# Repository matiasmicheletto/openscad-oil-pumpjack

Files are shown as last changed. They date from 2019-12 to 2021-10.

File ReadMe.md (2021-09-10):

# Parametric 3D model of an oil pumpjack

This is a Code-CAD based project that consists on the parametric modeling of all the parts of a scale oil pumpjack to be 3D-printed and driven by a 5V stepper motor. 

<p align="center">
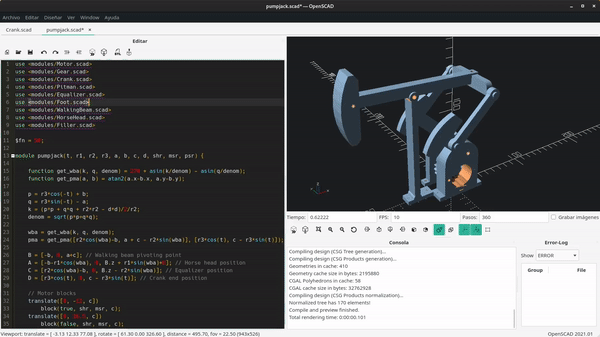
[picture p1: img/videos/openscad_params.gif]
Model
  
</p>

## Parameters of the model

This design is not based on any real model. Some basic parameters were selected to define the mechanical system dimensions.

<p align="center">
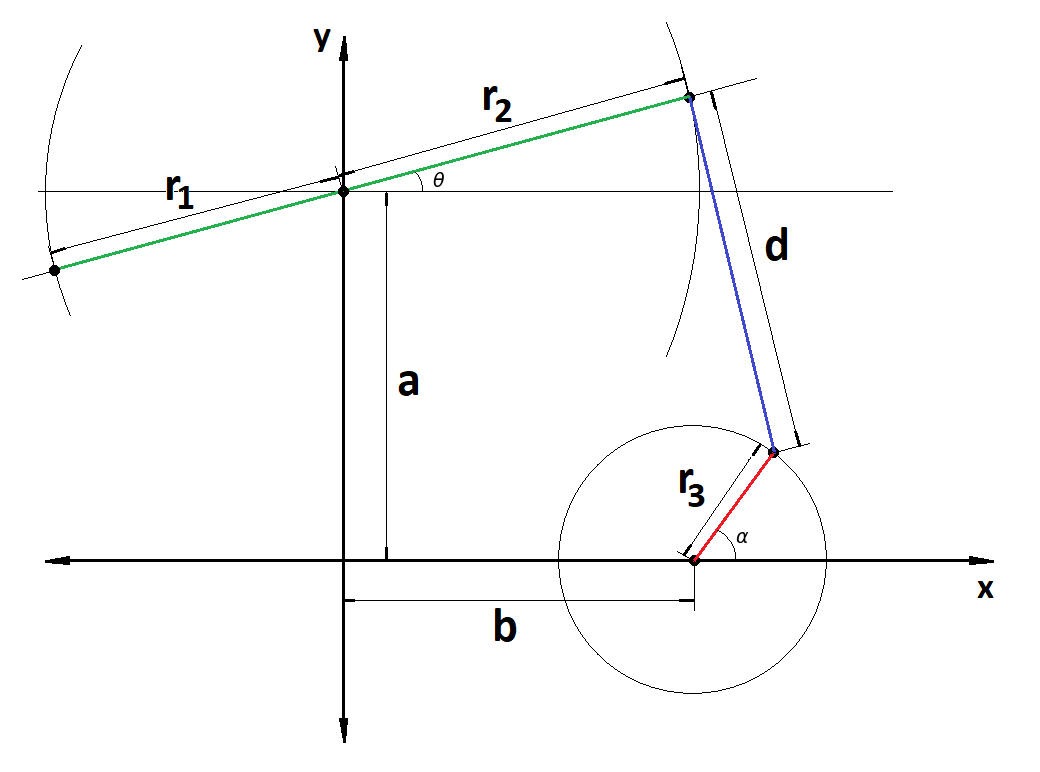
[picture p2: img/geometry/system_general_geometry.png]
Dimensions
  
</p>

An Octave simulation was used to test the resulting behavior of the machine depending on the selected parameters. The script was intended to optimize the design in some way and can be extended to perform a structural or a performance analysis.  

<p align="center">
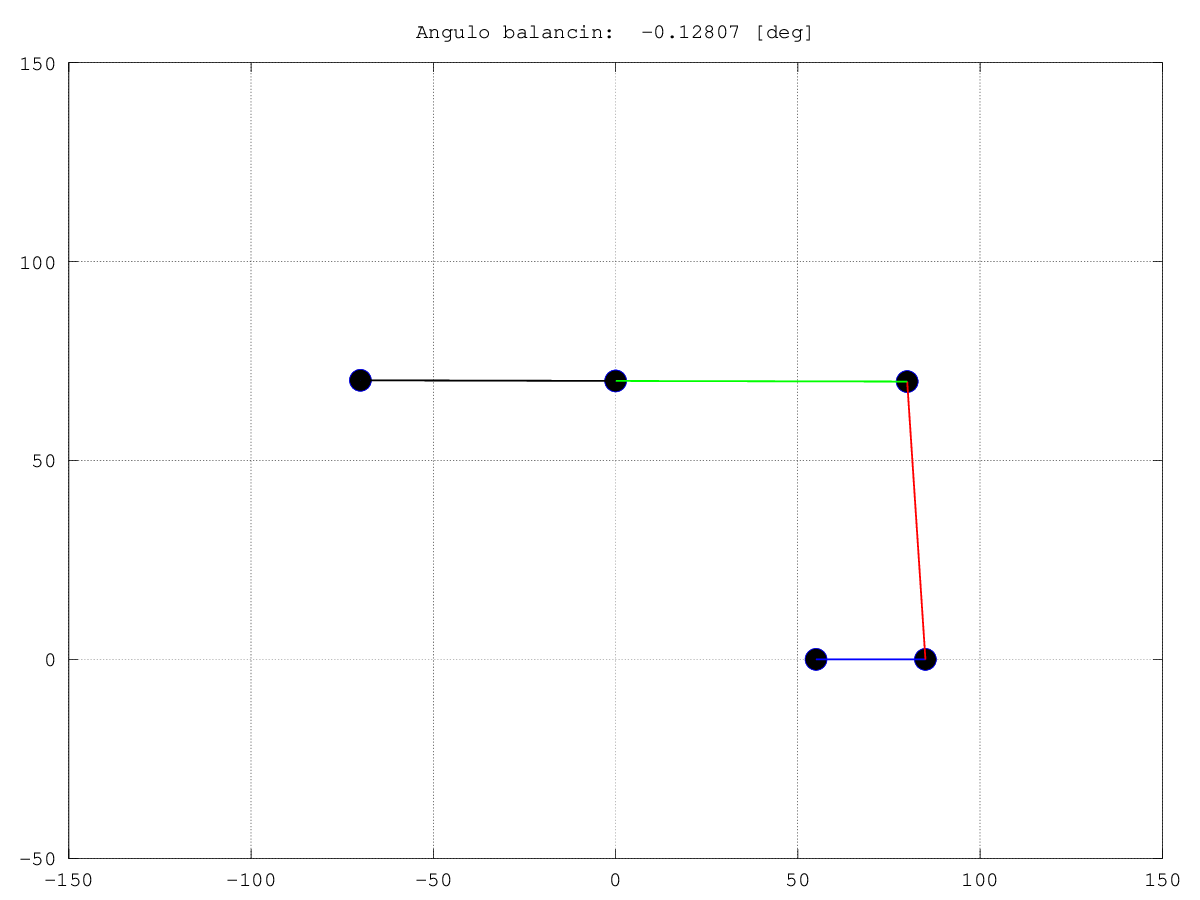
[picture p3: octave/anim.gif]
Simulation
  
</p>

## Electronics 

To control the stepper motor position and speed, it is provided the design of a four-step sequencer that uses a two-bit counter based on JK master-slave flip-flops (74HC109) and an AND-gate based decoder (74HC08). A ULN2003 based driver (not displayed in the schematics) was used to amplify the output current of the sequencer.  

<p align="center">
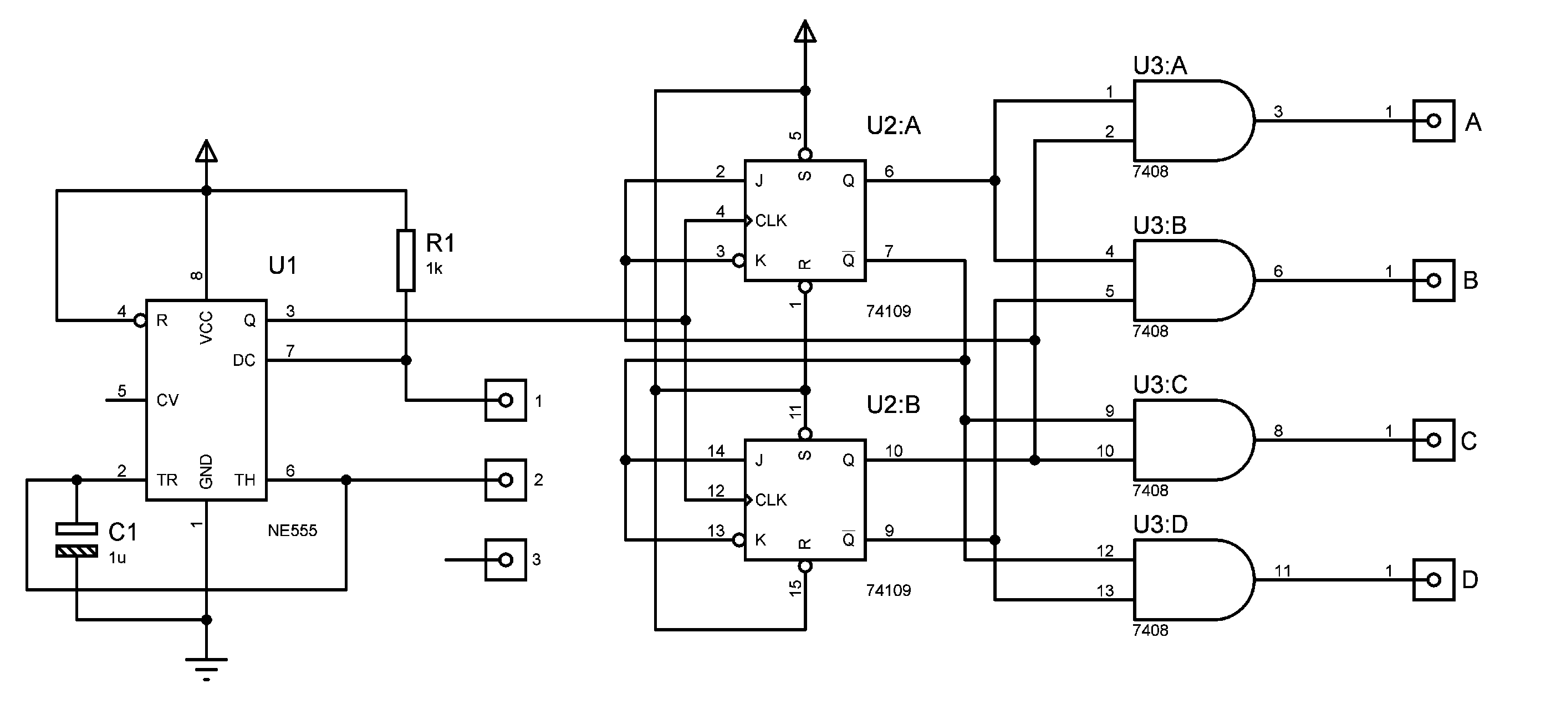
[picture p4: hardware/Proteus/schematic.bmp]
Schematics
  
</p>

This circuit was implemented on a perfboard. A CAD PCB design is also provided which follows the perfboard layout, however, its recommended to modify it to build a better design in order to achieve a more aesthetic result.

<p align="center">
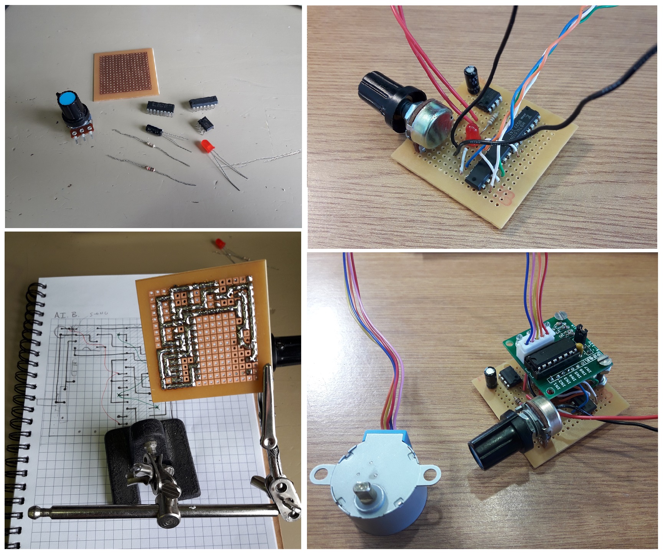
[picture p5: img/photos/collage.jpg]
Perfboard
  
</p>

## Printed model

The ready to print files are available in the [./stl](stl) folder.

<p align="center">
  Model
</p>

### Additional materials

  - 13 bolts M2.5 x 25mm  
  - 17 nuts M2.5  
  - 1 bolt M5 x 65 mm  
  - 5 nuts M5  
  - 4 thumbtacks  
  - 1 150x90x20 mm wood plank

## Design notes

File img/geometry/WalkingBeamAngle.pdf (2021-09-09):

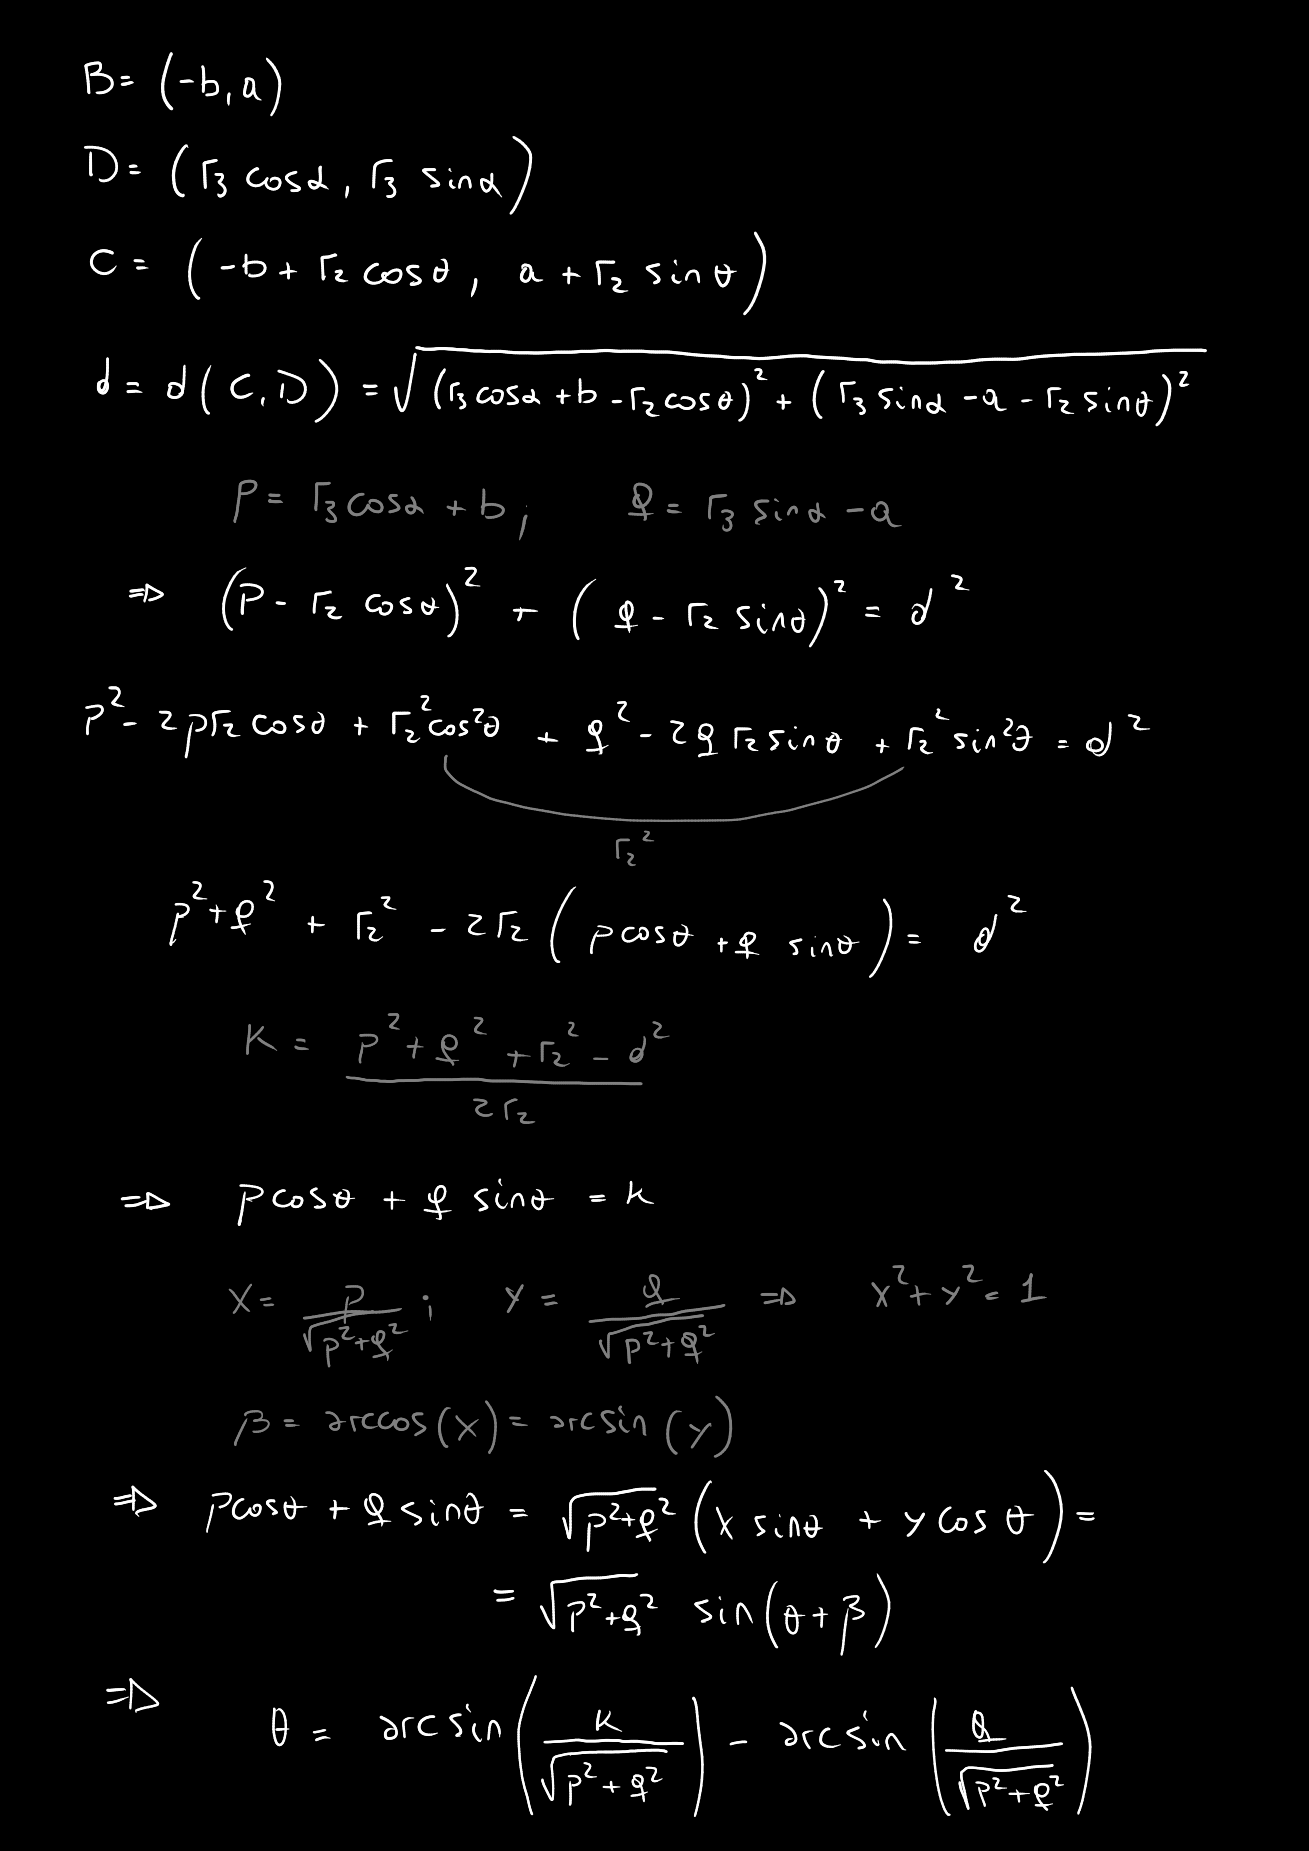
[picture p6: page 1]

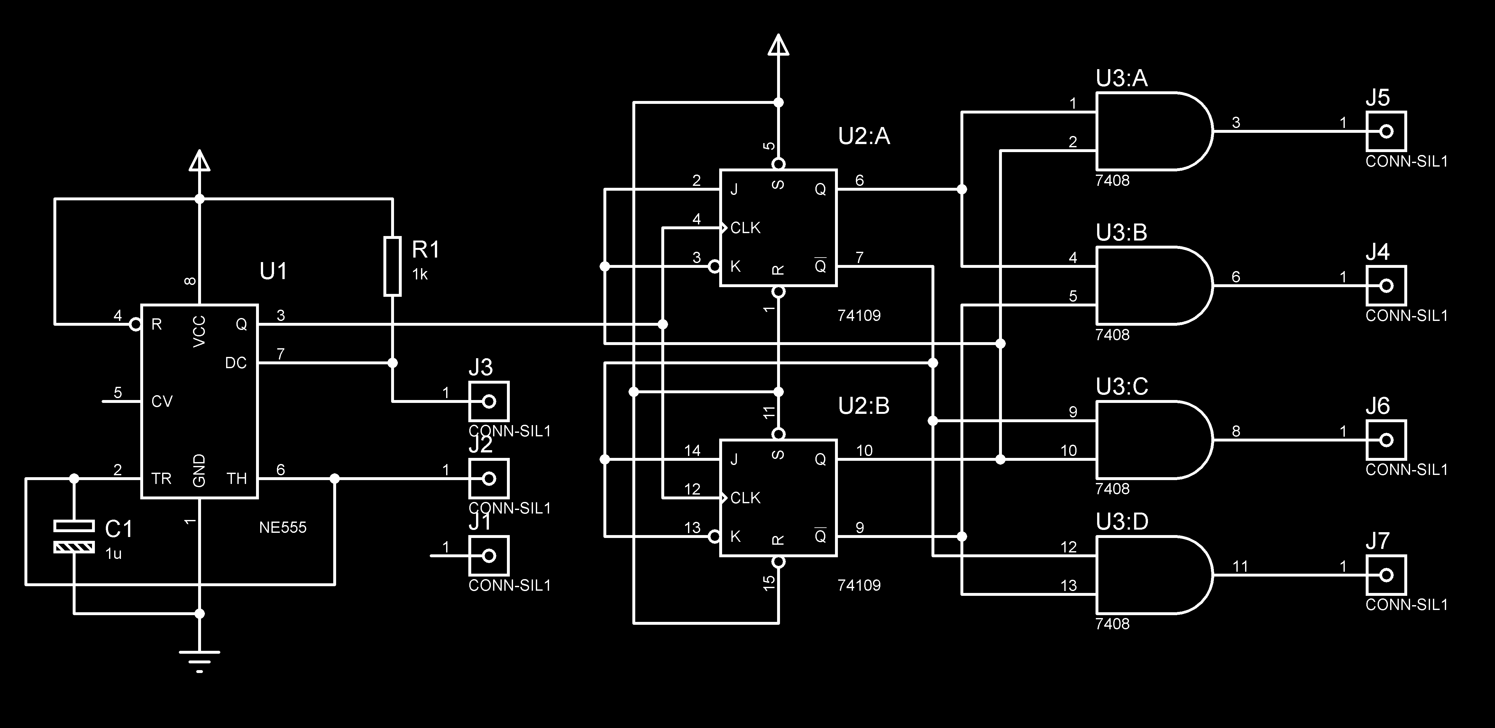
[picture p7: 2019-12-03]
hardware/Proteus/schematic_inv.bmp

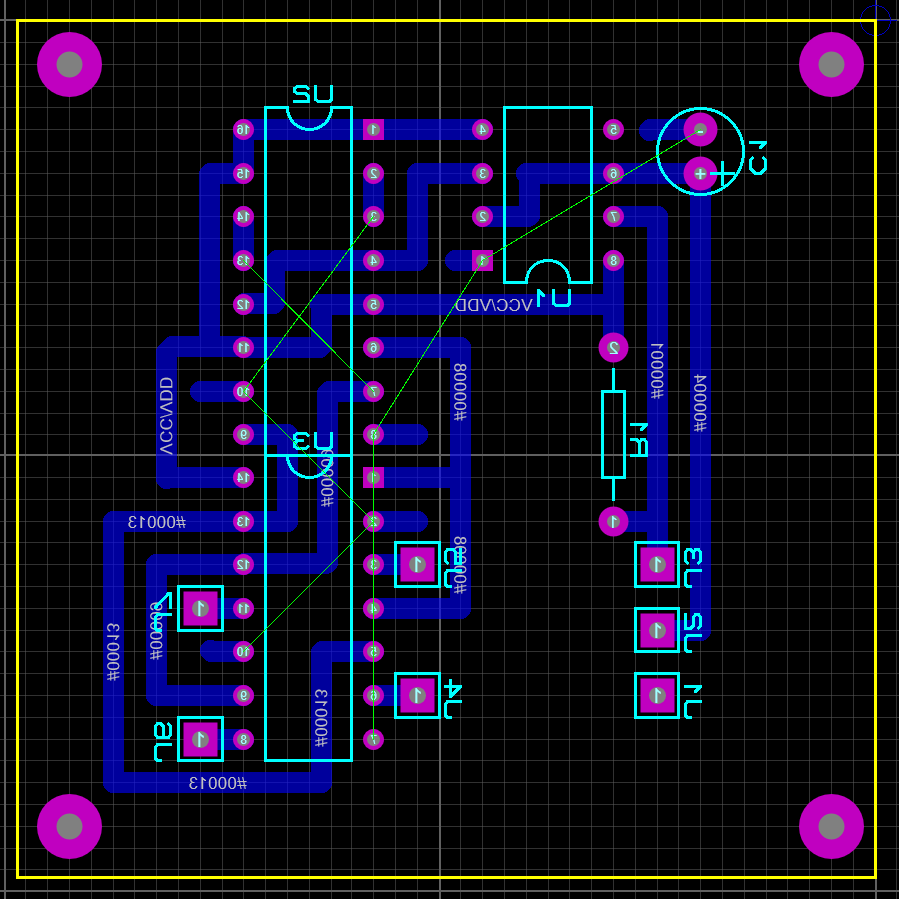
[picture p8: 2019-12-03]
hardware/Proteus/univ_pcb_mirror.png

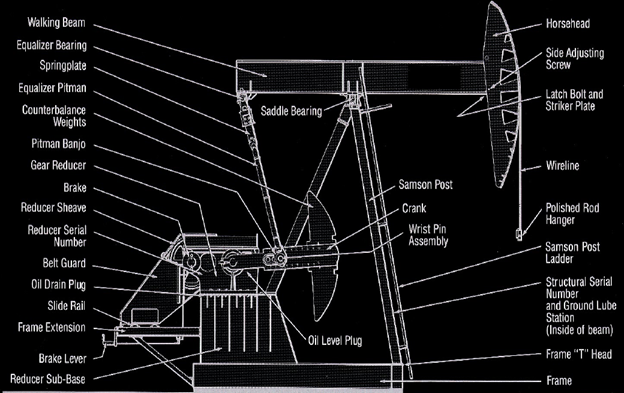
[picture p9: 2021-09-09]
img/geometry/pumping_unit_blueprints.png

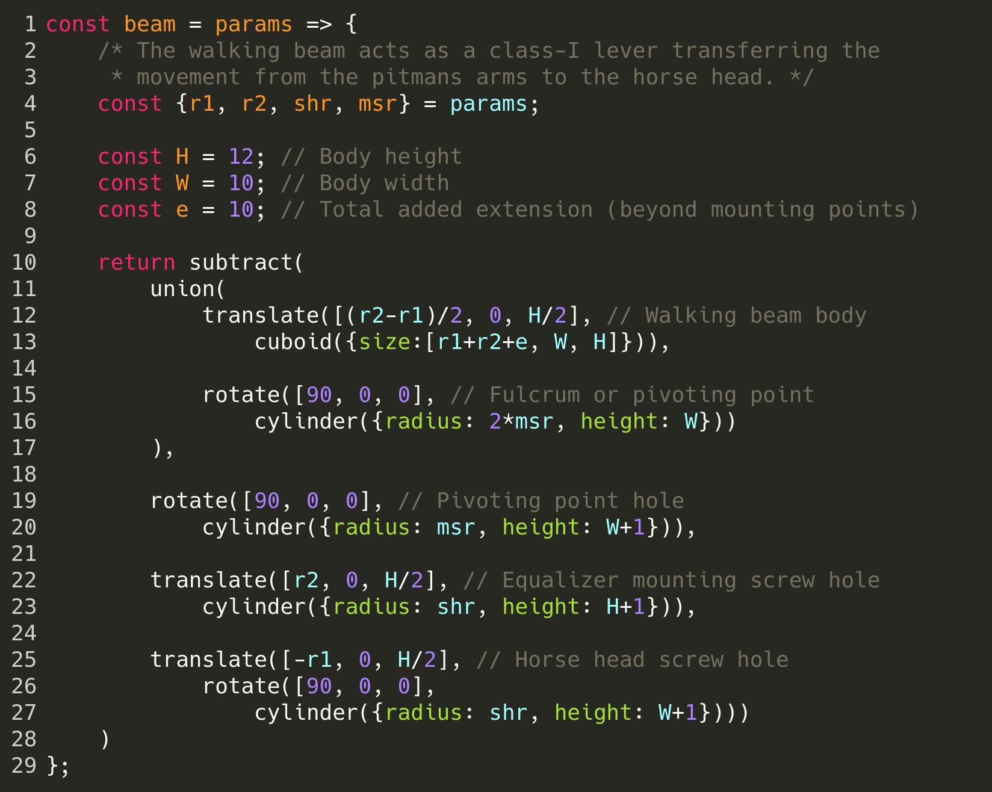
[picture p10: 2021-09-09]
img/screenshots/jscad_walking_beam.png

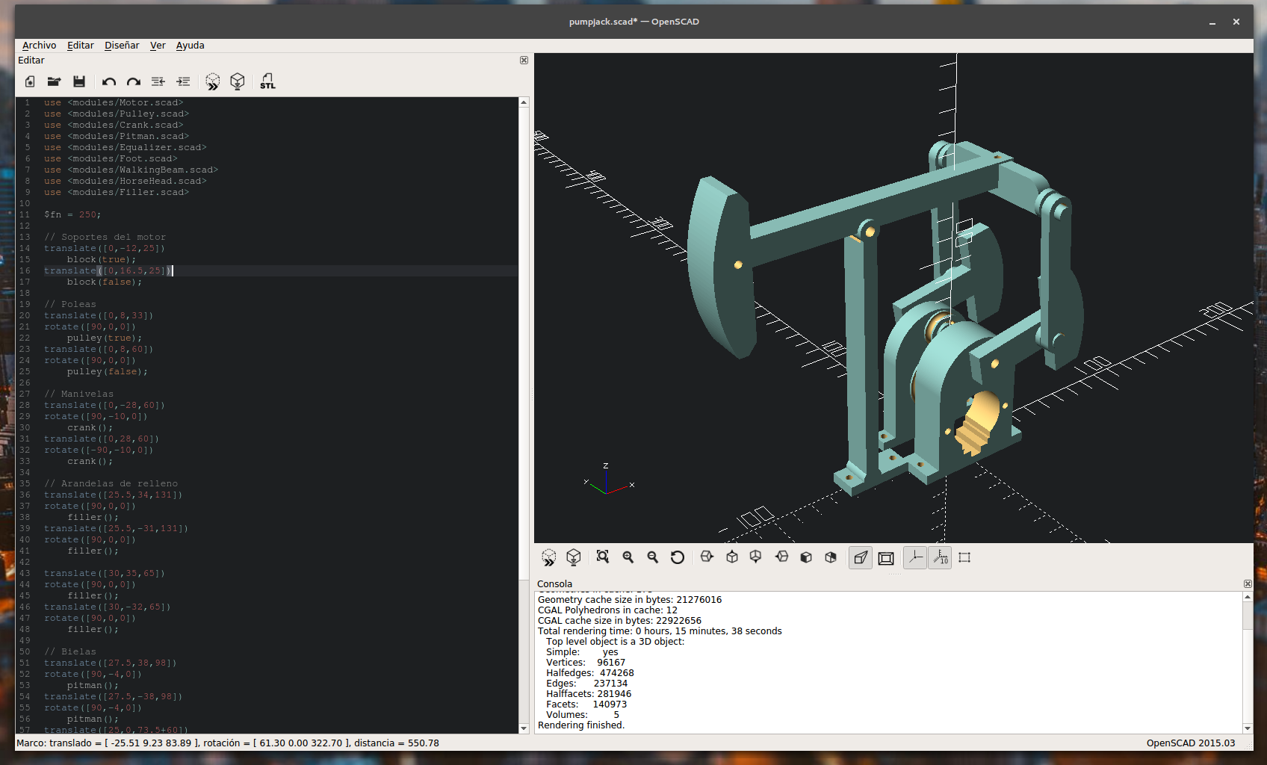
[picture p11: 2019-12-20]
img/screenshots/openscad_screenshot.png

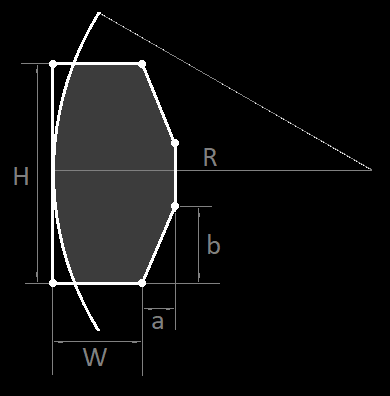
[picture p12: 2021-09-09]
img/geometry/horse_head_geometry.png

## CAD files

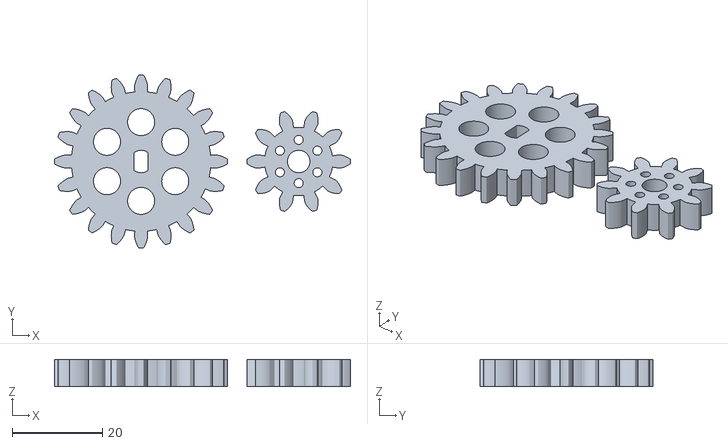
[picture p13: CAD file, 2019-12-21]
stl/Gears.stl
65.8 x 38.5 x 6.00

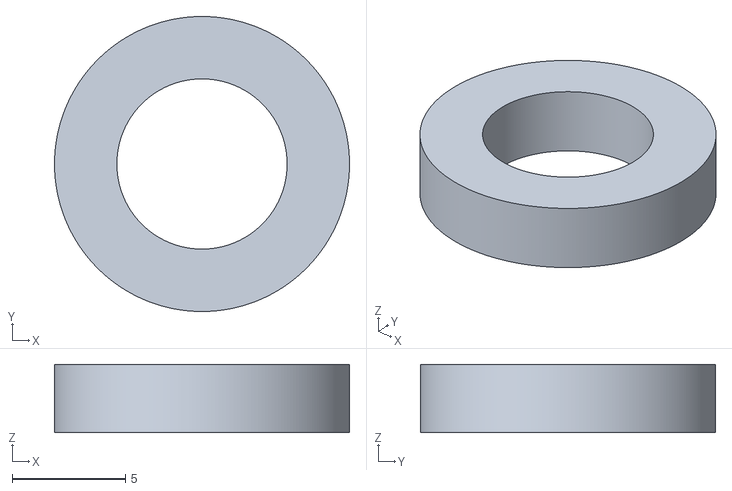
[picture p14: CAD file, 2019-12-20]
stl/Filler.stl
13.0 x 13.0 x 3.00

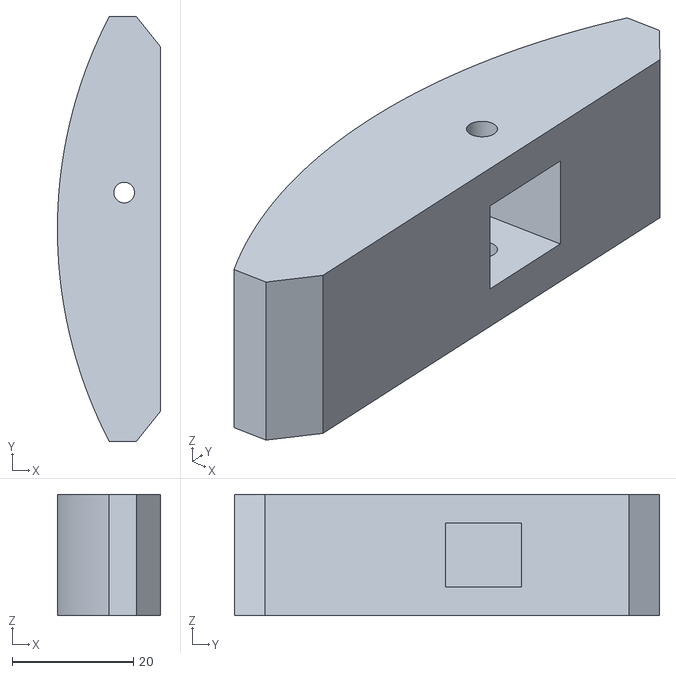
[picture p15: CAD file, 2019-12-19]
stl/HorseHead.stl
17.0 x 70.0 x 20.0

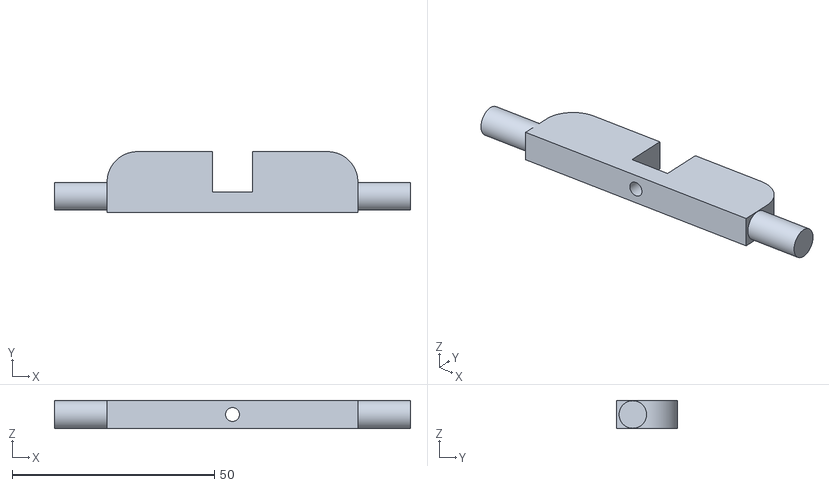
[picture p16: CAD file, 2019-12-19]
stl/Equalizer.stl
88.0 x 15.0 x 7.00

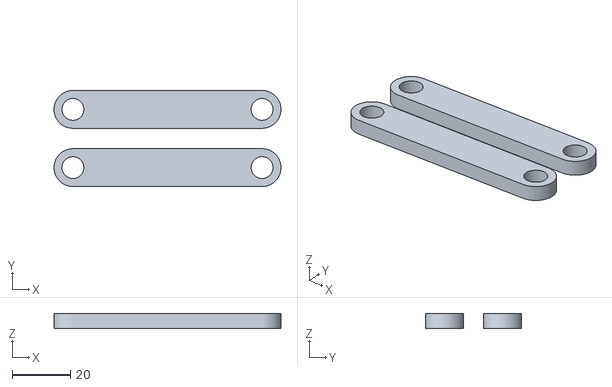
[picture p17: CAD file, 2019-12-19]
stl/Pitman.stl
78.0 x 33.0 x 5.00

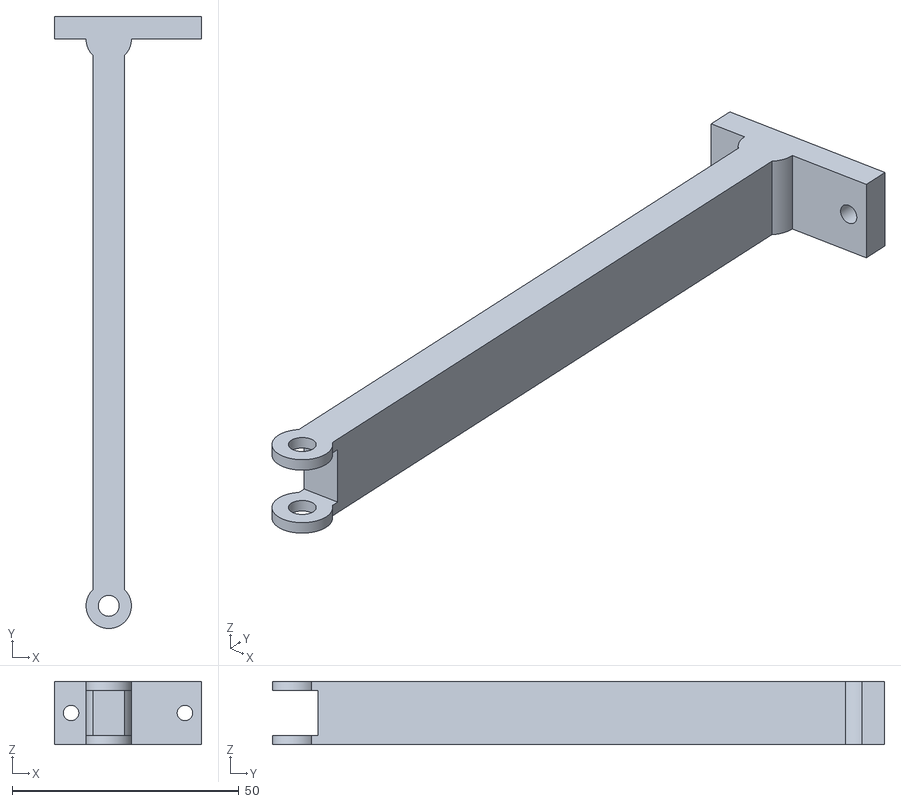
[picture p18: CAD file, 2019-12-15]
stl/Foot.stl
32.5 x 135.0 x 14.0

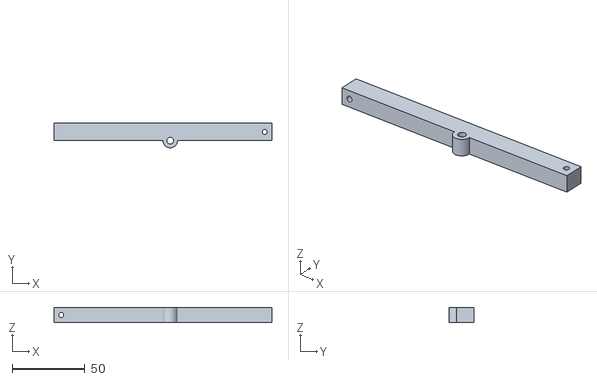
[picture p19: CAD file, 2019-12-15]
stl/WalkingBeam.stl
150.0 x 17.0 x 10.0

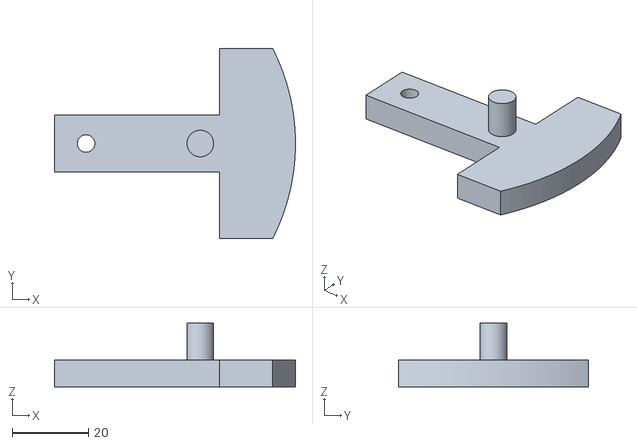
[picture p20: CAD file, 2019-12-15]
stl/Crank.stl
63.3 x 50.0 x 16.8

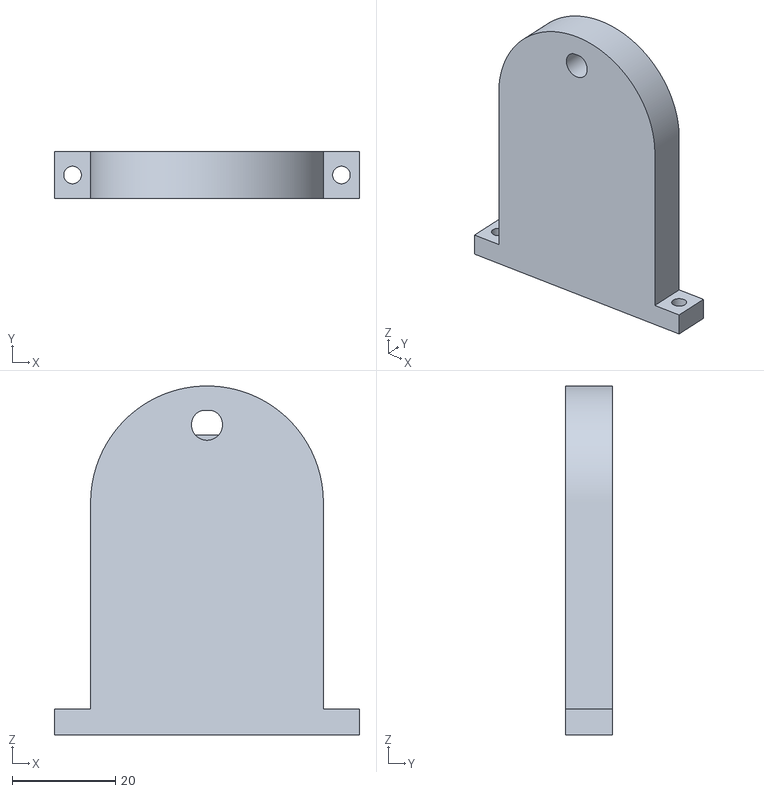
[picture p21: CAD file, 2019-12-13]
stl/Block.stl
59.0 x 9.00 x 67.5

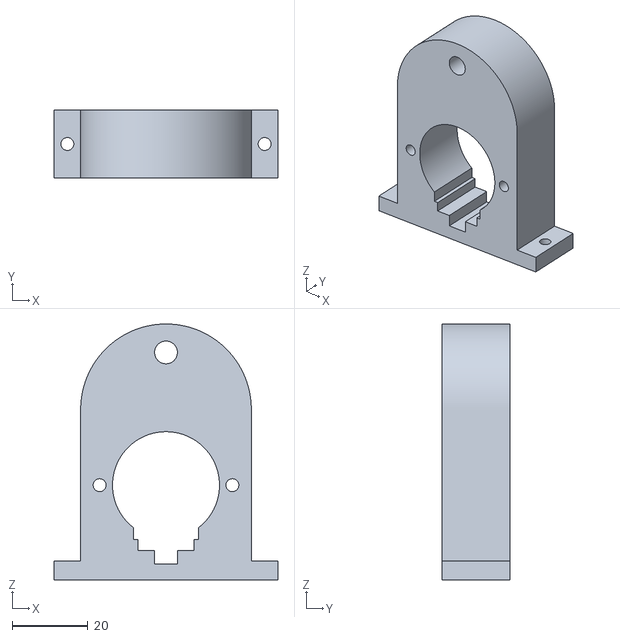
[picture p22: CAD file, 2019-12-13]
stl/BlockMotor.stl
59.0 x 18.0 x 67.5

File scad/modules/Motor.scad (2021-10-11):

module block(motor, shr, msr, c){ 
    /* A block to hold the stepper motor and main shaft */

    es = 15;    // Excentricity of the shaft hole
    L = 45;     // Width (X)    
    W = motor ? 18 : 9; // Length (Y)
    hh = 5;     // Mounting height
    H = c-es-hh;     // Height (Z)
    
    module envelope() {
        union(){
            translate([0, 0, -H/2-es])
                cube([L, W, H], center = true); // Envelope        
            
            // Rounded top
            translate([0, 0, -es])
                rotate([90, 0, 0])
                    cylinder(r = L/2, h = W, center = true);    
            
            // Mounting
            translate([0, 0, -H-hh/2-es])
                cube([L + 8*shr, W, hh], center = true); 
        }
    }
    
    module motor_hole() { // Space for motor placement
        Rm = 14 + 0.1;    // Motor radius
        d2 = 35;          // Distance between screw holes
        
        // Motor cable cover
        wc1 = 3 + 0.2;
        lc1 = 17 + 0.2;
        xc1 = sqrt(Rm*Rm-lc1*lc1/4)+wc1/2;
        wc2 = 5 + 0.2;
        lc2 = 14.5 + 0.2;
        xc2 = sqrt(Rm*Rm-lc2*lc2/4)+wc2/2;
        wc3 = 7;
        lc3 = 6;
        xc3 = sqrt(Rm*Rm-lc3*lc3/4)+wc3/2;
        
        union(){
            translate([0,0,-H/2-es])
                rotate([90,0,0])
                    cylinder(r = Rm, h = W+0.2, center = true);
               
            // Motor screw holes
            translate([-d2/2, 0, -H/2-es])
            rotate([90, 0, 0])
                cylinder(r = shr, h = W, center = true);    
            translate([d2/2, 0, -H/2-es])
            rotate([90, 0, 0])
                cylinder(r = shr, h = W, center = true);
            
            // Motor cable cover
            translate([0, 0, -xc1-H/2-es])
                cube([lc1, W, wc1], center = true);
            translate([0, 0, -xc2-H/2-es])
                cube([lc2, W, wc2], center = true);
            translate([0, 0, -xc3-H/2-es])
                cube([lc3, W, wc3], center = true);    
        }
    }
    
    module shaft_hole(){
        rotate([90,0,0])
            cylinder(r = msr+0.7, h = W, center = true);    
    }
    
    module screw_holes(){
        translate([-L/2-2*shr, 0, -H-hh/2-es])
            cylinder(r = shr, h = hh, center = true);    
        translate([L/2+2*shr, 0, -H-hh/2-es])
            cylinder(r = shr, h = hh, center = true);
    }

    difference(){ 
        color([.5,.5,.5])
        envelope();
        if(motor) motor_hole();
        shaft_hole();
        screw_holes();
    }
}

block(true, 1.7, 2.3, 60);
translate([0,28.5,0])
    block(false, 1.7, 2.3, 60);

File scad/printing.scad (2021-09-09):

use <modules/Motor.scad>
use <modules/Gear.scad>
use <modules/Crank.scad>
use <modules/Pitman.scad>
use <modules/Equalizer.scad>
use <modules/Foot.scad>
use <modules/WalkingBeam.scad>
use <modules/HorseHead.scad>
use <modules/Filler.scad>

$fn = 100;

module pumpjack(r1=65, r2=75, r3=30, a=60, b=50, c=60, d=65, shr=1.7, msr=2.3, psr=3.5) {
    // Motor blocks
    translate([0, -25, 9])
    rotate([90, 0, 0])
        block(true, shr, msr, c);
    translate([-50, 20, 4.5])
    rotate([90, 0, 180])
        block(false, shr, msr, c);
        
    // Cranks
    translate([5, 50, 3.5])
        crank(r3, msr, psr);
    translate([25, 70, 3.5])
    rotate([0, 0, 180])
        crank(r3, msr, psr);
        
    // Pitmans arms
    translate([50,-50,2.5])
        pitman(d, psr);
    translate([35,-50,2.5])
        pitman(d, psr);

    // Fillers
    translate([0, 87, 0])
        filler(psr);
    translate([20, 87, 0])
        filler(psr);
    translate([40, 87, 0])
        filler(psr);
    translate([60, 87, 0])
        filler(psr);

    // Equalizer
    translate([-20, -50, 3.5])
    rotate([0, 0, 90])
        equalizer(shr, psr);
        
    // Walking beam
    translate([70, 0, 12])
    rotate([180, 0, -90])
        beam(r1, r2, shr, msr);

    // Horse head
    translate([20, -70, 10])
    rotate([0, 0, 90])
        horseHead(r1, shr);

    // Samson post
    translate([85, 80, 7])
    rotate([90, 180, 0])
        foot(a, c, msr, shr);
        
    // Gear box
    translate([-50, 55, 0])
        gear(true);
    translate([0, 10, 0])
        gear(false);
}

pumpjack(65, 75, 30, 60, 50, 60, 65, 1.7, 2.3, 3.5);

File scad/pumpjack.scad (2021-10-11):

use <modules/Motor.scad>
use <modules/Gear.scad>
use <modules/Crank.scad>
use <modules/Pitman.scad>
use <modules/Equalizer.scad>
use <modules/Foot.scad>
use <modules/WalkingBeam.scad>
use <modules/HorseHead.scad>
use <modules/Filler.scad>

$fn = 100;

module pumpjack(t, type=1, r1=65, r2=75, r3=30, a=60, b=50, c=60, d=65, shr=1.7, msr=2.3, psr=3.5) {
    
    side = type==1 ? 1 : -1; // Inversion of sign for values of r3 and b
    
    // Parameters for compute the angles of moving parts
    p = side*(r3*cos(t) + b);
    q = -side*r3*sin(t) - a;
    k = (p*p + q*q + r2*r2 - d*d)/2/r2;
    denom = sqrt(p*p + q*q);    
    
    // Walking beam angle
    wba = (type==1 ? 270:90) + side*(asin(k/denom) - asin(q/denom));     
    
    B = [-side*b, 0, a + c]; // Walking beam pivoting point
    C = [side*(r2*cos(wba) - b), 0, a + c - side*r2*sin(wba)]; // Equalizer position
    D = [side*r3*cos(t), 0, c - side*r3*sin(t)]; // Crank shaft position

    // Pitmans arms angle (angle between equalizer and crank shaft)
    pma = atan2(C.x - D.x, C.z - D.z); 

    // Motor blocks
    translate([0, -12, c])
        block(true, shr, msr, c);
    translate([0, 16.5, c])
        block(false, shr, msr, c);

    // Gear box
    translate([0, 8, c-28])
    rotate([90, -t/2, 0])
        gear(true);
    translate([0, 8, c])
    rotate([90, t, 0])
        gear(false);
        
    // Cranks
    translate([0, -28, c])
    rotate([90, t,0])
        crank(r3, msr, psr, type);
    translate([0, 28, c])
    rotate([-90, t, 0])
        crank(r3, msr, psr, type);
    
    // Fillers
    translate([C.x, 34, C.z])
    rotate([90,0,0])
        filler(psr);
    translate([C.x, -34, C.z])
    rotate([90,0,0])
        filler(psr);
    translate([D.x, 34, D.z])
    rotate([90,0,0])
        filler(psr);
    translate([D.x, -34, D.z])
    rotate([90,0,0])
        filler(psr);
    
    // Pitmans arms
    translate([D.x, 38, D.z])
    rotate([90, pma, 0])
        pitman(d, psr);
    translate([D.x, -38, D.z])
    rotate([90, pma, 0])
        pitman(d, psr);
    
    // Equalizer
    translate(C)
    rotate([0, wba, 0])
        equalizer(shr, psr);
        
    // Walking beam and horse head
    translate(B)
    rotate([0, wba, 0])
        union(){
            beam(r1, r2, shr, msr, type);
            translate([type == 1 ? -r1:-r1-r2, 0, 6])
            rotate([90, 0, 0])
                horseHead(type == 1 ? r1:r1+r2, shr); 
        }
    
    // Samson post
    translate([B.x, 0, 0])
    rotate([0,0,type==1 ? 0: 180])
        foot(a, c, msr, shr);
}


// Conventional
translate([0,50,0])
    pumpjack(360*$t, 1, 65, 75, 30, 60, 50, 60, 65, 1.7, 2.3, 3.5);
// Mark II
translate([0,-50,0])
    pumpjack(360*$t, 2, 30, 80, 20, 60, 50, 60, 65, 1.7, 2.3, 3.5);

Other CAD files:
scad/modules/Crank.scad
scad/modules/EngineHolder.scad
scad/modules/Equalizer.scad
scad/modules/Filler.scad
scad/modules/Foot.scad
scad/modules/Gear.scad
scad/modules/GearGenerator.scad
scad/modules/HorseHead.scad
scad/modules/Pitman.scad
scad/modules/Pulley.scad
scad/modules/WalkingBeam.scad

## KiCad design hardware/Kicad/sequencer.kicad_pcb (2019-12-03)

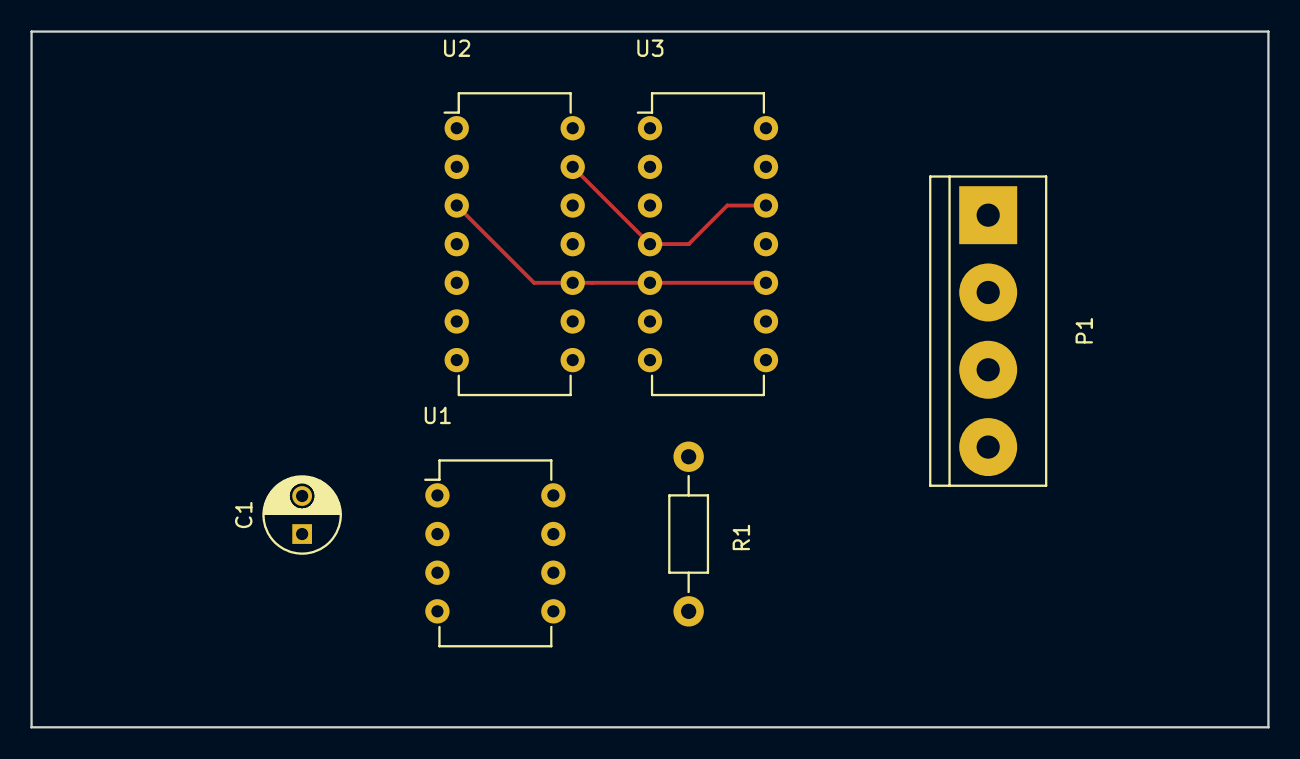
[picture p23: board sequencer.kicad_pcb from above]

Board: 2 copper layers, 81.3 x 45.7 mm, 6 parts (0 on the bottom side), 13 nets.

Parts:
C1: CP_Small; C_Radial_D5_L11_P2.5
P1: CONN_01X04; bornier4
R1: R_Small; Resistor_Horizontal_RM10mm
U1: LM555N; DIP-8_W7.62mm
U2: 74LS109; DIP-14_W7.62mm
U3: 74LS08; DIP-14_W7.62mm

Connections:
GND: C1.2, U1.1, U2.8, U3.7
unnamed: C1.1, U1.2, U1.6
unnamed: P1.1, U3.3
unnamed: P1.2, U3.6
unnamed: P1.3, U3.8
unnamed: P1.4, U3.11
unnamed: R1.2, U1.7
unnamed: U1.3, U2.4, U2.12
unnamed: U2.6, U3.1
unnamed: U2.9, U3.2, U3.13
unnamed: U2.2, U2.3, U2.10, U3.5, U3.10
unnamed: U2.7, U2.13, U2.14, U3.4, U3.9, U3.12
VCC: R1.1, U1.4, U1.8, U2.1, U2.5, U2.11, U3.14

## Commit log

2019-12-03 Primer commit
    [EngineHolder.scad, MotorPulley.scad, SmallPulley.scad]
2019-12-03 Piezas soporte mecanismo accionamiento
    [EngineHolder.scad, EngineHolder.stl, MotorPulley.scad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]
2019-12-03 Disegno electronico Kicad (sin terminar) y Proteus (para plaq. univ.)
    [hardware.kicad_pcb, hardware.sch]
2019-12-04 Primera impresion 3D
    [EngineHolder.scad, EngineHolder.stl, MotorPulley.scad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]
2019-12-09 Modelo scad cabezal. Renombre archivos. Imagenes modelo
    [EngineHolder.scad, HorseHead.scad, sequencer.kicad_pcb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]
2019-12-11 Desplazamiento del acople cabezal. Simulaciones octave para calibrar medidas
    [HorseHead.scad]
2019-12-11 Optimizacion de la simulacion
2019-12-12 Modelos como modulos independientes
    [Crank.scad, EngineHolder.scad, HorseHead.scad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]
2019-12-13 Dimensiones definidas. TODO: aplicar a todas las piezas
    [Crank.scad, EngineHolder.stl, HorseHead.scad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]
2019-12-13 Nuevas medidas. TODO: Soporte del balancin
    [Crank.scad, HorseHead.scad, Motor.scad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]
2019-12-15 Ajuste dimensiones. Pie soporte balancin. Presentacion partes
    [Crank.scad, Equalizer.scad, Foot.scad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]
2019-12-15 Disposicion de piezas para impresion
    [printing.scad]
2019-12-15 STL de cada pieza
    [Block.stl, BlockMotor.stl, Crank.stl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]
2019-12-19 Ajuste diametro eje bielas. Gif animado con Python.
    [Pitman.scad, Pitman.stl]
2019-12-19 Fix medidas cabeza de mula y ecualizador
    [Equalizer.scad, Equalizer.stl, HorseHead.scad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]
2019-12-20 Arandelas de relleno para ecualizador y manivelas
    [Filler.scad, Filler.stl, printing.scad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]
2019-12-20 Lista de materiales
2019-12-21 Reemplazo de las poleas por engranajes
    [Gear.scad, GearGenerator.scad, Gears.stl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]
2019-12-23 Actualizacion stl de todas las piezas
2021-08-22 Traduccion Readme, script y algunos modulos
    [Crank.scad, Equalizer.scad, Filler.scad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]
2021-08-29 Translated comments
    [Crank.scad, Equalizer.scad, Filler.scad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]
2021-08-31 Crank and Equalizer implementations in JScad
    [Crank.scad, pumpjack.scad]
2021-09-03 Block, Fillers and Pitmans arms implementations in JScad
    [Motor.scad]
2021-09-06 Jscad implementation of all parts. GUI for parameter configuration
    [HorseHead.scad]
2021-09-06 JScad model: print layout switcher
2021-09-09 Openscad animated model
    [Crank.scad, Equalizer.scad, Filler.scad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]
2021-09-09 Printing layout update
    [printing.scad, pumpjack.scad]
2021-10-10 Mark II (3rd class lever pumpjack)
    [Crank.scad, WalkingBeam.scad, pumpjack.scad]
2021-10-11 Mark II and horse head geometry fixes
    [HorseHead.scad, pumpjack.scad]
2021-10-11 Couloured parts
    [Crank.scad, Equalizer.scad, Filler.scad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]
